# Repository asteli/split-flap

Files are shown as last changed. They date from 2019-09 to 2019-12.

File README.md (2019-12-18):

# split-flap
A mechanical split-flap display in the style of the Solari boards, designed to be modular, manufacturable, and low-cost.

Each module consists of a control PCB, a stepper motor (NEMA 17), mounting bracketry, and wheel made from 3D-printed and laser cut parts, holding 60 custom-printed and laser cut character cards.

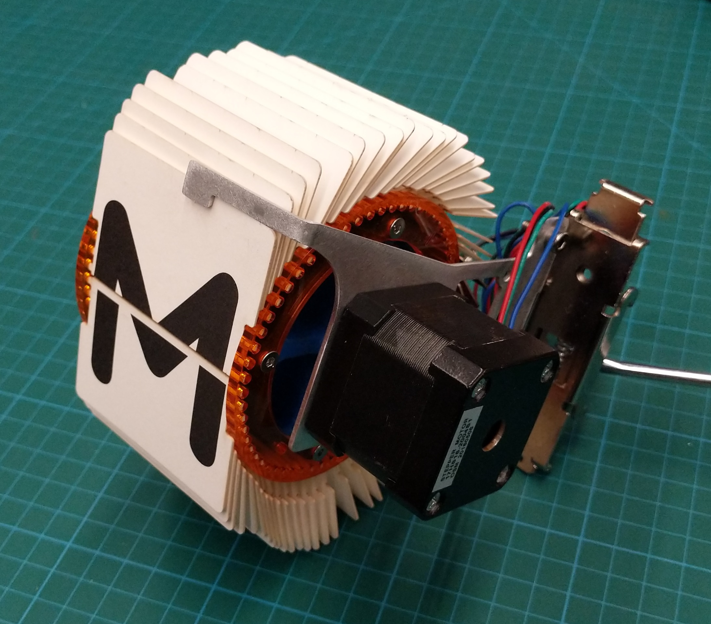
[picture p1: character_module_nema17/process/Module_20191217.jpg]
An assembled module, sans PCB, off of DIN rail.


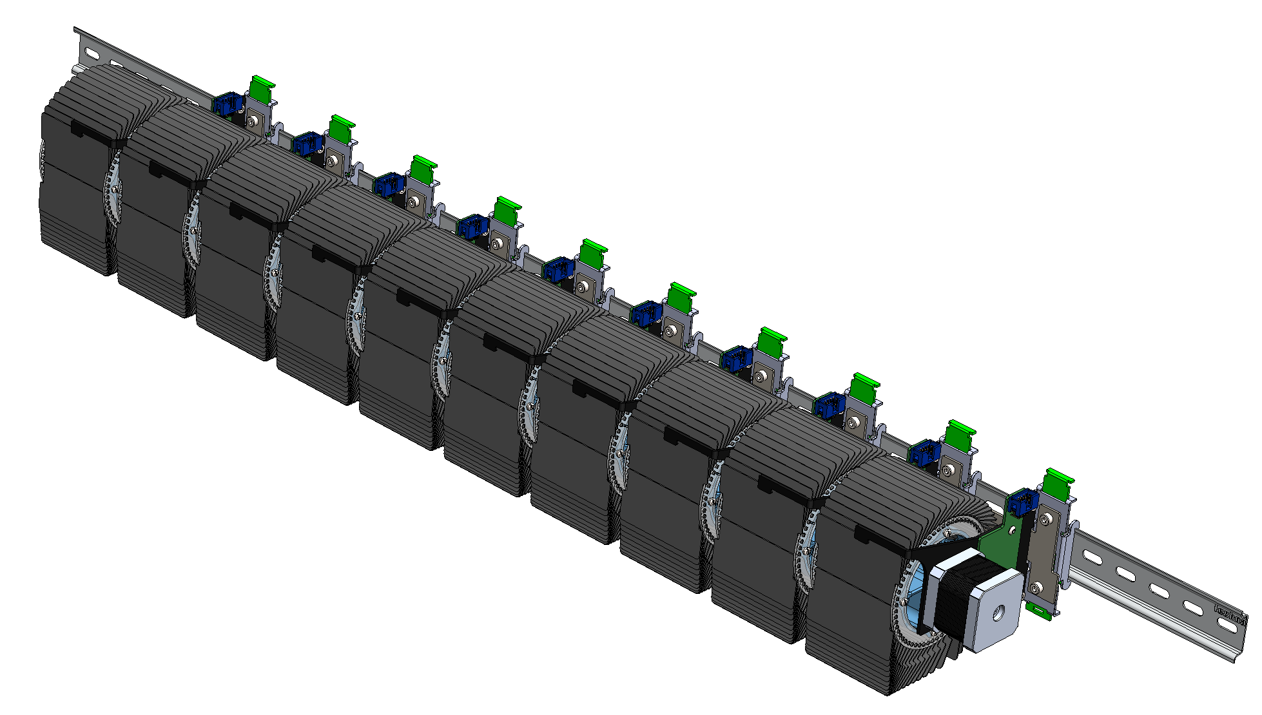
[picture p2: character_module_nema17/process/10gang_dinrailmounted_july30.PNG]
A 10-module wide section of a split-flap display


[Quick video of an early prototype running open-loop](https://youtu.be/AlwcM3Y5v3c) 

The V2 is designed around a NEMA 17 motor, which paradoxically is much cheaper than the NEMA 08. Likely because it enjoys wide use in 3D printers and the like. They cost something like 5-8 USD wholesale. A friend happens to have a few hundred sitting around from an old project, which makes the choice even harder to resist.

The V2 also features a much larger character size (usable character area is roughly 60mm x 60mm -- old flaps were ~35mm wide), and is designed to be DIN rail mountable and powered/controlled via a common rail and bus for simplicity and reliability. The part count has come down significantly -- I've removed the (2) external bearings, as the NEMA 17 motor is large enough that I can trust its bearings to cope with the modest lateral loads involved.

When you are planning on building even 20 of something, every last part counts against you.

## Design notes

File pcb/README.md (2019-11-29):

# PCBA Design Notes:

## Requirements:
	- Small microcontroller (AVR ATMega, STM32F0)
	- Single IDC connector for common bus data and power
		- I2C(sda,scl)[2], V_motor[3], V_logic[2], GND[5]
	- Hall effect sensor for indexing
	- DIP switches to set address
	- Stepper motor driver IC
	- (optional pop) - RST and CALIB switches
	- sundry LEDs
	- PMIC (Vmot -> V_logic (3.3V))
	- PTC or other input protection (we're common bus yo! gotta be careful)
	- ESD and other protection

## Parts Selected:
	MCU 	- ($1.93/1pc) STM32F030C8T6TR 
	DIPSW 	- ($0.98/1pc) 8pos, SMD, TE CONN. 1-1825058-9
	DRIVE 	- ($3.11/1pc) A4988
	PMIC 	- ($0.83/1pc) DC-DC Buck AOZ1282CI (12 -> 3.3V) (investigate cheaper chinese parts at some point)
			- (solution cost $3?)
	HALL 	- ($0.40/1pc) Toshiba TCS40DPR
	LEDs	- ($0.26/1pc) LTST-C190GKT (0603 Green)
			- ($0.26/1pc) LTST-C190KRKT (0603 Red)
	CONN 	- ($1.56/1pc) Molex 0901303112 . 12POS Rectangular header, shrouded+keyed, R/A
				- Alt: 	5-102617-4 TE Connectivity AMPMODU II line, $2.53/1pc
	TACSW 	- ($0.12/1pc) Panasonic EVQ-Q2B03W

	So far we're looking at ~$15 in components? Maybe $5 for the PCB and $5 for assy/board? (Maybe wishful thinking)

## MCU Functionality:
	In no particular order:
		- Listen to I2C, filter incoming messages and display character corresponding to address
		- Calibration functionality - tacsw advances cards until hallsw, zeroes counter, slowly rotates until operator releases button 
		at the index card. index card position stored in NVM.
		- DIPSW translates to address
		- Control registers accessible by I2C in direct-addressed mode. LEDs, calibration, motor settings, character maps
		- Standby current control (or shut off driver IC entirely if that works mechanically and doesn't cause glitching to adjacent 
		characters)
			- This can be accomplished using a couple I/O and voltage divider ladder to get the voltages we want. Will have to tune the resistor values but easy to use 1 I/O to set RUN vs STDBY current.

## MCU I/O Pin Counts:
	- [2] I2C
	- [8] DIP switch configuration
	- [8] A4988 Motor controller (nSleep, step, ms1:3, dir, nEnable, nReset)
	- [2] A4988 V_ref control
	- [2] LEDs
	- [1] User switch
	- [1] Hall sensor

	Looks like ~24 I/O min? Cheapest that'll fit? STM32F030K6T6, with 26 I/O. ($1.62/1pc, CT)

	Next up in the price lineup is STM32F030C8T6TR, with 39 I/O, at a whopping $1.93/1pc, cut tape.

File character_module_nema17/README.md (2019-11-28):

## TODO:
- Build new character flap vector files. Old flap vectors split each character between the front and back of the print, causing character-half registration issues.
- Spec and design module control PCBA
- Print and laser cut new flaps
- Waterjet and bend prototype bracket, validate bracket design

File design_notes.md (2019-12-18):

# SplitFlapClock Design Notes

## December 17, 2019
Waterjet and bent the bracket. Used 0.0615 aluminum, only because that's what was in the scrap bin that was large enough. It's a bit flimsy like that, should use 0.080 at least. Fitment is OK, the arm on top actually seems to have the side-effect of ratcheting the hub, as the flaps sort of deform into a V shape, catching and preventing the hub from rotating backwards. I might keep that.

Torque on the motor seems pretty reasonable, although I could probably move the retention arm out another millimeter and reduce the torque/power requirement/wear on cards (probably).

## December 1, 2019
The KiCad libs available are pretty nice. Haven't had to make any schematic symbols myself yet. Digikey has nice libs available, and the KiCad official lib seems pretty expansive as well. Good job everyone!

## November 29, 2019
Toying with the idea of using the STM32F0 itself to create the stepper waveforms. Sounds trivial but I would need a way to sense phase current. That would potentially reduce the unit cost by $2? The FETs could be quite small at these powers. The issue then is that I would be committing to engineering a motor controller, which... well, maybe let's leave that for the cost optimized version of this module. I do like the idea though.

DIP SW: use int PU res, allow DIP to short to GND. 

## November 28, 2019
Status update:
	- Staying with NEMA 17.
	- Staying with a PCB per module
	- I'm going to use DIP switches to set addresses, because my previous scheme seems like a pain in the ass and the ease of confiuration with DIP switches is worth the extra cents. 

I'm starting the PCB design. Looks fairly simple. Going to be all DIGIKEY parts for this first build, I can try to go and cost optimize (chinese domestic components and assy) later. I wonder if I can find a vendor for the steel plates.

Spec'ing PCB parts is coming along. I'm going to try to get a really solid architecture together before actually building things.

So much of the time I see hardware/firmware/mechanicals being developed independently of each other, but here I have the option of thinking through the entire design, tip to tail, which is nice.

## September 16 2019

CAD for the newest version is mostly done. Have the mounting plate mostly designed up but I am going to simplify the geometry a bit to make it slightly easier to manufacture.

I am also looking at evaluating the 28byj-48 geared stepper motor in conjunction with a uln2003, apparently a popular configuration for small and low power actuation. 
	This motor appears to be quite small and have limited torque. Its max speed is something like 15RPM (0.25 Hz) which is more than fast enough for a split flap display. 

VW has loads of stepper motors he doesn't need. They are not D-flatted, which doesn't mean much in my application. I need to figure out how to size the bore of my hub to be a press fit that doesn't take massive amounts of force to attach/detach. Going slightly loose is an option as I can always use an adhesive (RTV? CA glue?) to retain it if the slip fit is a bit oversize.

## July 30 2019

Looking at using i2c for communications. Assuming 0.5A for 1 module, 7A continuous max amperage for 22AWG, that gives us 14 modules per power conductor pair. So doubling up (2x 24V, 2x PGND) gives us a decent amount of headroom. I want to use IDC connectors, just because fabricating the cable will be as simple as punching down a bunch of connectors on a shared ribbon, and it minimizes passthrough/daisy-chain failure modes. I was looking at a serial retransmit scheme like WS2812s or APA102s but I think this will be more reliable.

Question is how to assign i2c addresses to submissive devices. Scheme is as follows:

There _is_ a daisy chained "strobe" signal -- wait that doesn't work because we're using common bus IDC and ugh

OK how about maybe using prop delay? Naw sounds flakey.

Could do the classic i2c dip-switch or solder-blob jumper thing. Could do 6 bits, 64 permutations... should be good enough for anyone, right?

Tac switch on each device that when pushed, queries the bus for taken addresses, then assigns itself to the first open slot. Then saves its address to eeprom. Need an address reset mechanism, maybe by resetting uC with the "address set" switch depressed.

Then when the primary controller powers up, it scans the bus for available secondaries and assumes that they're physically in order from left to right.

Doing i2c means that a raspi or something can be in charge of setting all the things, which means application code can be in python or something. Plug a LORAN modem into the UART and bam, long distance wireless.

Only needs to be set up once. We can also have modules ident using their built in single-character displays.

Issue in the model: my SOT23 hall-effect sensor sits about 5mm away from the outer surface of the flap disk. I would much rather it be something like 2mm. I guess I could just use a longer magnet... was spec'ing a 1/16" (Thick) x 1/8" (Diam) magnet before, could use a 1/8"x1/8" and that closes the gap by 0.3175/2 = 1.56 ish mm. goes down to 3.5mm. more reasonable. I think I can live with that. OK crisis averted. I am slightly worried about magnetizing my screws, in which case the hall effect sensor could pick up the screws as well as the magnet. Maybe use SS screws there. Or don't magnetize them I guess.

Going to design a plate that links up with the DIN clip. It will set spacing and add a little bit of torsional stability to the assembled modules.

## July 29
I think I want to build the character displays in 4 or 5-gang modules. 20-gang is going to be super huge. 4-gang seems like a fun clock sized size. 5 would also work.
This would also be a good size for having one PCB control a number of them and not have insane looking harnesses running around. 

Local VMOT24 -> 5/3.3V for logic.

Connectivity:
UART
Ethernet
Power -- possible to do PoE? What's our PD? It's easy and cheap to do the typical powerpole terminals however.

TODO:
	- Retention tab

	- Model module mounting solution
		- DIN rail brackets?
		- DIN rail
	- Hall effect sensr
		- p/n
		- model
		- location
		- magnet location
	- PCB
		- location
		- functionality
		- connectivity

## June 3:

Other bearings came in. Pressed all the stuff together, forgot to align the flat on the motor shaft, broke the spokes out of the hub. 

That aside, there's still massive eccentricity in my otherwise round parts. I think I probably need to orient them such that they print with the rotational axis nearly straight up, despite the risk involved.

Other issues: Clearance between rotating parts. The further the material gets from the rotation axis or the fixing bearing, the more likely it is to rub. Keep clearances wide open if it doesn't affect functionality. No lost pride in having some air in the design.

The motor is indeed strong enough to rotate the display, but just barely. Eccentricity causes uneven lateral forces on the shaft that result in binding at one part of the rotation. Solution? Reprint hub.

Bearing seat were also rather tight. They did eventually fit but I think I want to add another 50 micron or more to the radius of the large seats. It's easy to get a bearing not to spin in a seat, lot easier than removing material to get it to press in.

Also, adding deep chamfers (1+ mm ) to the first edge of the bearing seat should help with getting them pressed in perpendicular in the first place. Use a press...

There was minimal issue putting the inserts in. May be a good idea to deepen the bores they go into. Chamfer couldn't hurt.

Oversizing the motor slot by 100um. Can glue it in just as easily. Little CA'll do ya.

Going 100um oversize on the bearing bore (up from 50um oversize). 

Added a little recess for a tiny chunk of retroreflector to sit in.

Todo on the enclosure:
Find a way of affixing the leaf that doesn't look like jank
Remove the slot and tab stuff from the front.
Enlarge the hole for the motor connector access.
Get rid of the leaf spring entirely and just use the acrylic to detain the flaps.

Todo on the motor mount:
Bore deeper for the inserts
Chamfer the outside edge at the far end of the motor

Todo on Flaps:
Generate Template for cutting

Mid July:
Ditched the old design. The motor was a bit small for what it was doing, and worse, NEMA 08 motors are expensive. I'm moving to a NEMA 17 motor, which can be had for $5 a piece perhaps (and VW has a lot, 400 something of these motors just sitting around).

Redesigned, removing the near and far end bearings -- the bearings in the motor itself are now big enough to handle the radial loads. This brings down part count significantly.
Also I'm going to ditch the per-module enclosure, and modify the design such that the motors nest inside the adjacent hubs. Per-module structure goes from:

Acrylic enclosure
Motor mount block
Motor mount bearing
Motor NEMA 08
Hub
Hub disks
Flaps
Far end bearing
Far end bearing block

To:
Sheet metal bracket
Motor NEMA 17
Hub
Hub disks
Flaps

Also I'm downsizing the flaps disks from 1/8" acrylic down to 1/16" because it's cheaper and the loads involved are very small. This will allow me to squeeze PHSCHS or SHCS screws in to fasten the disks, meaning that I don't have to counter sink those self-tapping M2.5 clearance holes.

## May 29

Loaded the models into preform. I tweaked the printed parts to use brass M3 threaded inserts instead of screwing directly into the plastic. Had to increase the size of a couple parts in order to make that work.

I'm going to screw directly to the hub to attach the acrlic flap retainer disks.

Laying out the components in Preform, I'm making sure to orient the parts to keep most if not all of the support structure touchpoints out of the bearing areas so that we don't get interference when I try to press the bearings in.

## May28

Added the encoder. Shortened the flaps just slightly, looks like it can't jam now. Not sure about what material to use for the flaps still. Acrylic likely too brittle. Thinking delrin or PET?

Ordered all materials. Came out to $200. Haven't worked out the spring thing bit yet. Considering harvesting the steel clip off of a pen to make the first article.

## May 27 2019

Aspect ratio of the flaps is interesting. Making them long makes the space needed to do the angle reversal after the card is displayed bigger, and thus drives part of package size.

I'm noticing that certain design choices are ... convergent. Like having the tabs on the sides of the flaps, or having a certain aspect ratio in order to get the packaging to make sense. (taller flaps mean the whole enclosure has to get taller to give them space at the bottom of the loop)

I'm envisioning an even less expensive design for light duty use that uses DC gearmotors and a grey code optical encoder printed on the side of the hub. uC on the back has just one FET to turn the motor on, and reflectivity pickups. If sensors don't see the right code for the commanded character, spin the motor.

The bearings are massive overkill as well. For a clock sort of function a set of low friction plastic or brass bushings would work great. Very little load. I'm going to use ball bearings because they're what I know. Also they look pretty slick.

I'm not quite sure yet how I want to do the control. One way would be to have a separate controller on each module and daisy chain them a la serially addressable LED chains. You'd need a host somewhere that could spit UART at the modules. Do we want checksums here? Is that overkill? There are super low-tech ways to go about the control. If one was willing to index using an encoder of some kind, it's certainly possible to use basic logic gates and a DC gearmotor to servo to a position encoded as binary or BCD over 6 logic bits. Very 80s. Maybe next rev.

I'm going to need to cut the lower lip of the front opening on the enclosure down low enough that the flaps can't jam up against it. sort of a liability as it stands now, the rotor could push the flaps down into it and sieze the mechanism. Maybe shorten the flaps ... again ... if the enclosure cut looks untenable.

I just realized I can install the encoder or reflectometer or whatever -- the positioning thingy into the far side bearing block. Got loads of space there and I can make a cut in the side of the casing just like for the motor wires. Don't think there's enough space to put an actual full encoder on there right now, although I could distribute the sensors throughout the disk around the bearing. But that's an unwieldy solution, to say the least.

Rotate the bearing block holes 180 and put two screw holes in the block to attach a PCB, add corresponding void in the LH enclosure plate, run wires to the PCB out back. Echo Zulu. Reflecto-dot can go on the hub itself, or optionally the disk. Each one could probably benefit from calibration at time of programming.

### Questions:

The stepper motor I'll probably be using is a NEMA 8 (0.8" square section), with a 1.8 degree full step size. That doesn't really line up nicely with the 6 degree increments between symbol changes. I can use microstepping to even out the rotation. I might have to leave the motors on all the time to keep the rotor at an unnatural resting spot between steps. Also possible that backlash in the mechanism will absorb the last fraction of a rotation after the stepper is powered off. If it ends up being an issue I may have to bite the proverbial bullet and go up in motor size up to a NEMA11 to get a stepper with an 0.9 degree step size. While not exactly a clean divisor, that gives me nearly 7 steps per symbol change. It would also make the entire mechanism a lot bigger. Boo.

How to size tab-and-slot construction for the acrylic enclosure? Can I use nominal dimensions and hope that the laser cutter's kerf takes care of the clearance for me?

What about sizing bores for bearings? I don't know how far off-nominal the housings are going to be. Does it make sense to oversize the bores so that there's maybe a bit of slop, then to fill it in with adhesive? Or to leave it nominal dimension and try and press-fit them? Will that crack the printed plastic parts?

How much bending compliance can I expect from the flaps? Is the retention mechanism that we're using to do the "detent" more reliant on the flap bending or the retention tab bending? Can I use the enclosure itself to do the flap detention?

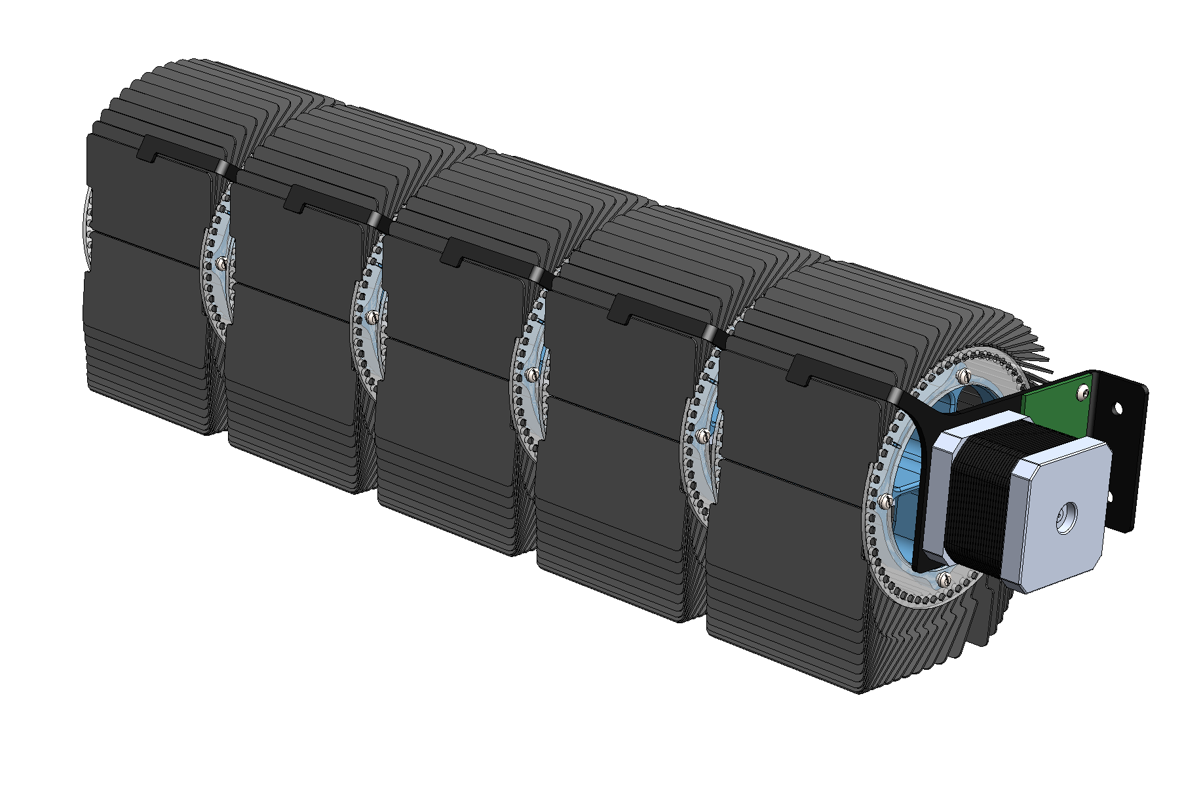
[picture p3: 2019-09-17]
character_module_nema17/process/5gang_motorside_20190729.PNG

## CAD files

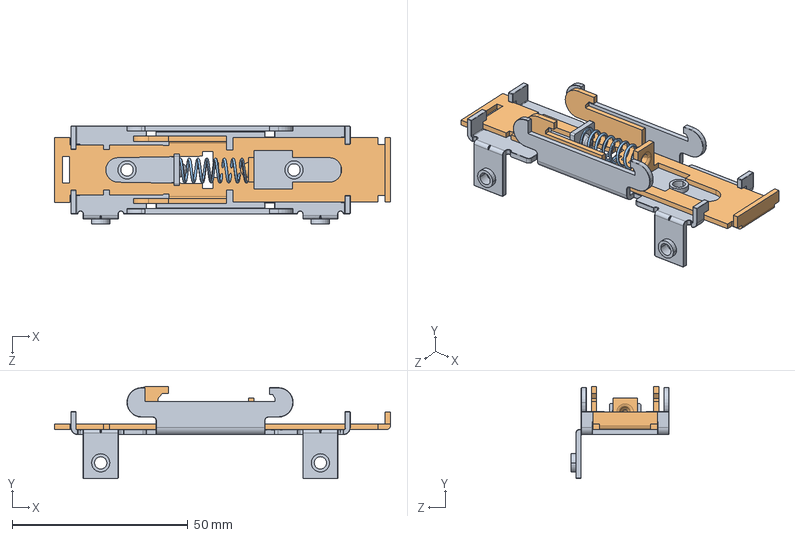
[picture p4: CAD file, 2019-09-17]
character_module_nema17/DINM30/Clip, DIN, Winford DINM30.SLDASM
95.6 x 26.3 x 27.9 mm
DINM30-Clip.step
DINM30-Shell.step
DINM30-Spring.step

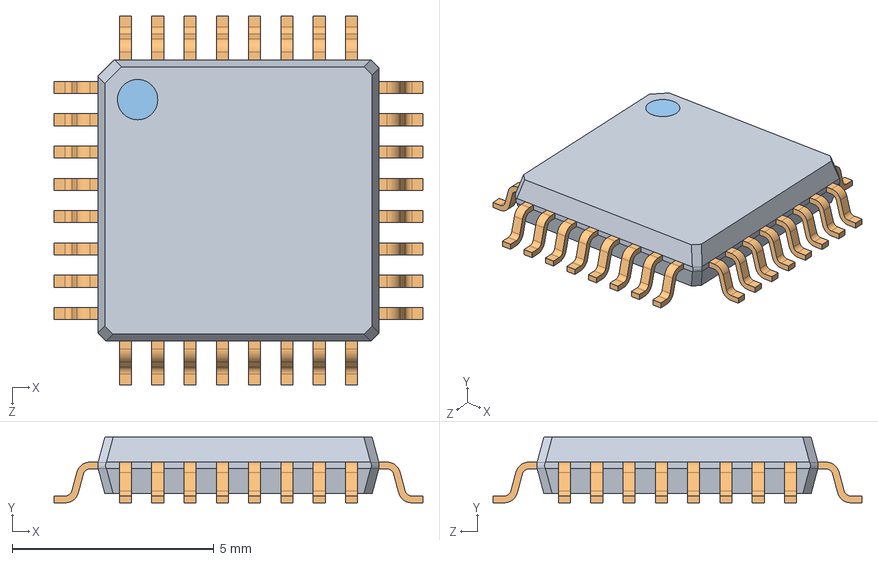
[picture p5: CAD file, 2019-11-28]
character_module_nema17/Electrical Components/LQFP32/User Library-LQFP32-2.sldasm
9.14 x 1.63 x 9.14 mm
User Library-LQFP32-2_case
User Library-LQFP32-2_pin x 32
User Library-LQFP32-2_circle

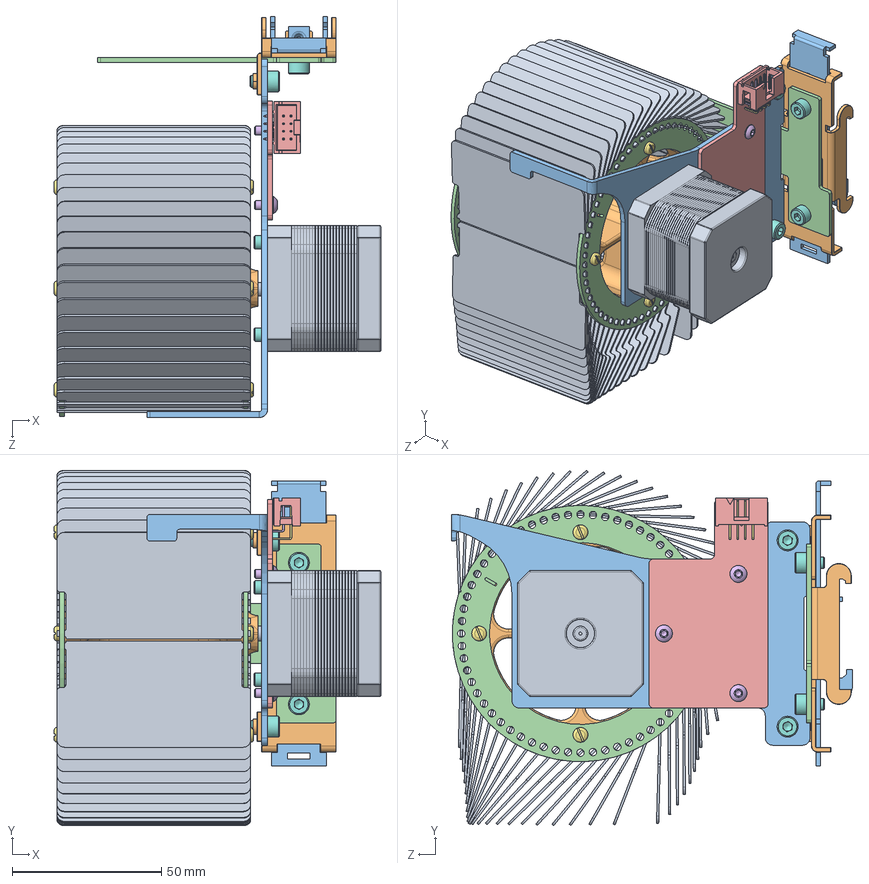
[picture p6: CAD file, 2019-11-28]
character_module_nema17/Subassembly, Character Module.SLDASM
109.7 x 119.3 x 134.6 mm
Motor, Stepper, Nema 17
Hub, Flap Carrier
Bracket, Motor Mount
Disk, Flap Retainer x 2
PCB, Local Driver Board, Outline
socket button head cap screw_am x 3
pan head tapping screw_am x 8
socket head cap screw_am x 8
Split Flap x 60
DINM30-Clip.step
DINM30-Shell.step
DINM30-Spring.step
71965_Y08.stp
71953_X03.stp x 4
71953_X04.stp x 4
User Library-LQFP32-2_case
User Library-LQFP32-2_pin x 32
User Library-LQFP32-2_circle
SOT-23
Plate, Module Spacer

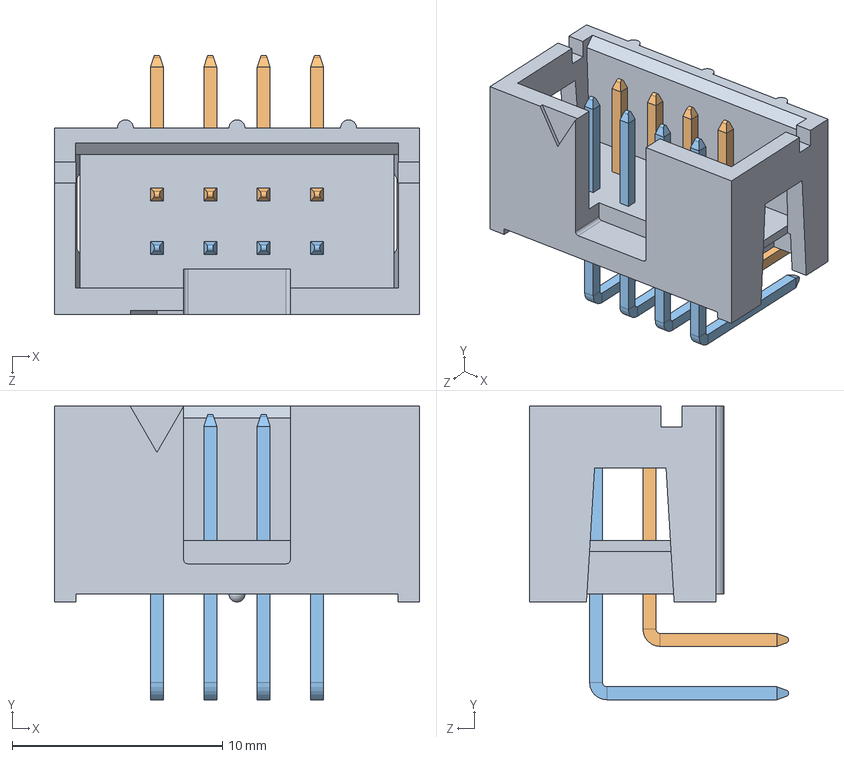
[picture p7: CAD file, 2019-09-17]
character_module_nema17/Connector/Connector, Header IDC, 8 Position, Right Angle, Shrouded, 75867_y32_asm.SLDASM
17.4 x 14.0 x 12.3 mm
71965_Y08.stp
71953_X03.stp x 4
71953_X04.stp x 4

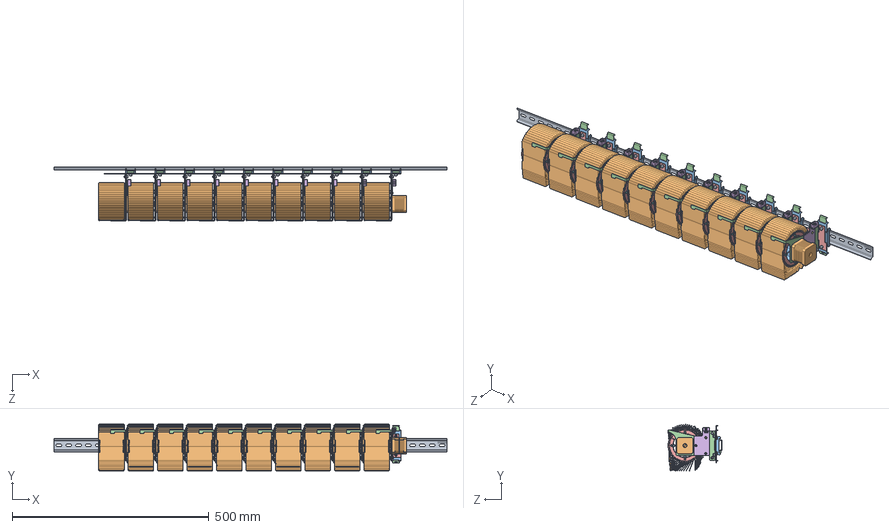
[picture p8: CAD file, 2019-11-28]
character_module_nema17/Assembly, Character Display.SLDASM
1000.0 x 119.3 x 137.7 mm
DIN Rail, 1m, TECHNA_TTEC CA701
Motor, Stepper, Nema 17 x 10
Hub, Flap Carrier x 10
Bracket, Motor Mount x 10
Disk, Flap Retainer x 20
PCB, Local Driver Board, Outline x 10
socket button head cap screw_am x 30
pan head tapping screw_am x 80
socket head cap screw_am x 80
Split Flap x 600
DINM30-Clip.step x 10
DINM30-Shell.step x 10
DINM30-Spring.step x 10
71965_Y08.stp x 10
71953_X03.stp x 40
71953_X04.stp x 40
User Library-LQFP32-2_case x 10
User Library-LQFP32-2_pin x 320
User Library-LQFP32-2_circle x 10
SOT-23 x 10
Plate, Module Spacer x 10

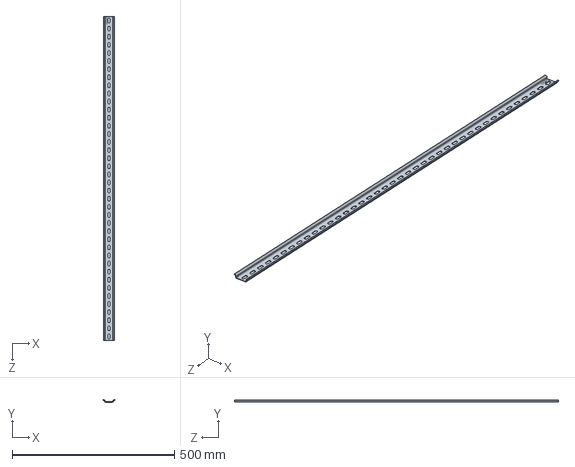
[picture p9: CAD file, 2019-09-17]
character_module_nema17/DIN Rail/DIN Rail, 1m, TECHNA_TTEC CA701.SLDPRT
35.0 x 7.50 x 1000.0 mm

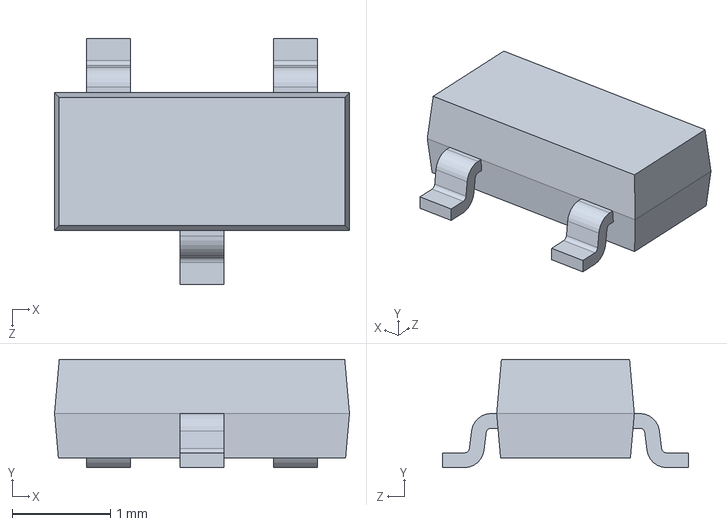
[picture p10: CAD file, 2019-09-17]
character_module_nema17/Electrical Components/SOT23/SOT-23.SLDPRT
3.00 x 1.10 x 2.50 mm

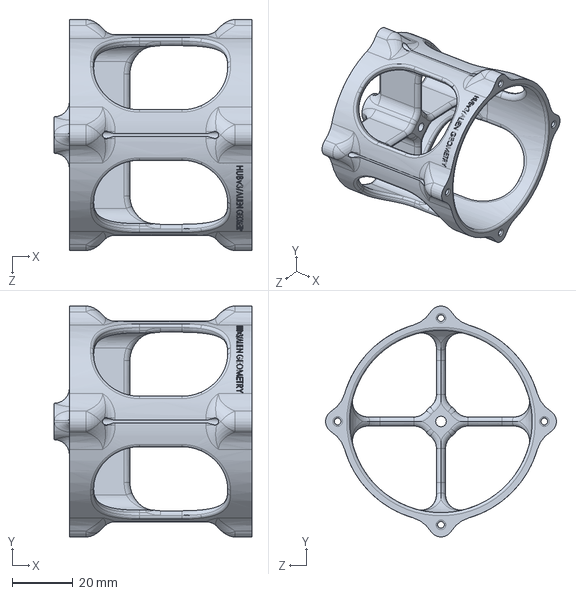
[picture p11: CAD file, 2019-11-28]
character_module_nema17/Hub, Flap Carrier.SLDPRT
65.0 x 76.0 x 76.0 mm

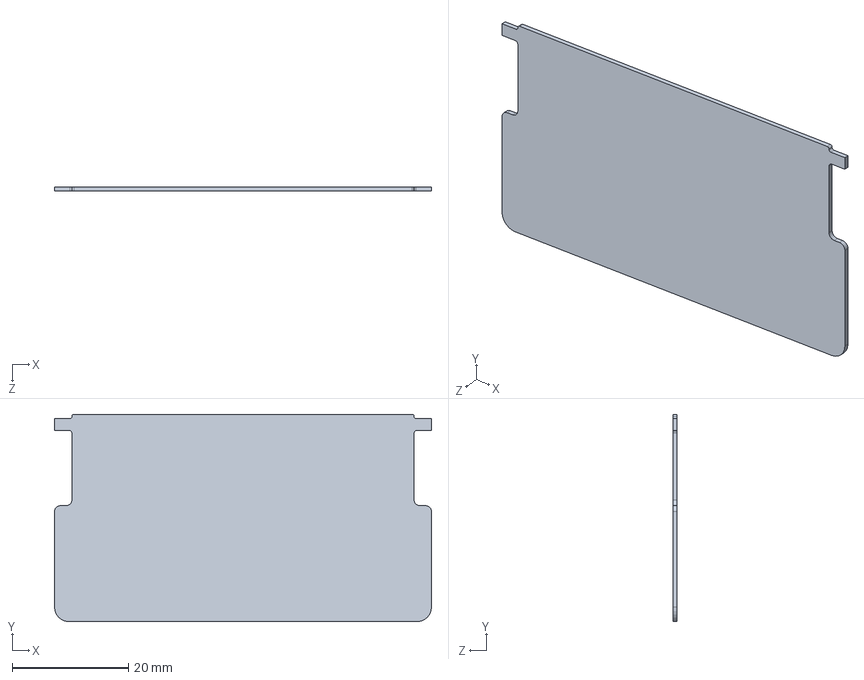
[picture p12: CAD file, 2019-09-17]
character_module_nema17/Split Flap.SLDPRT
65.0 x 35.8 x 0.762 mm

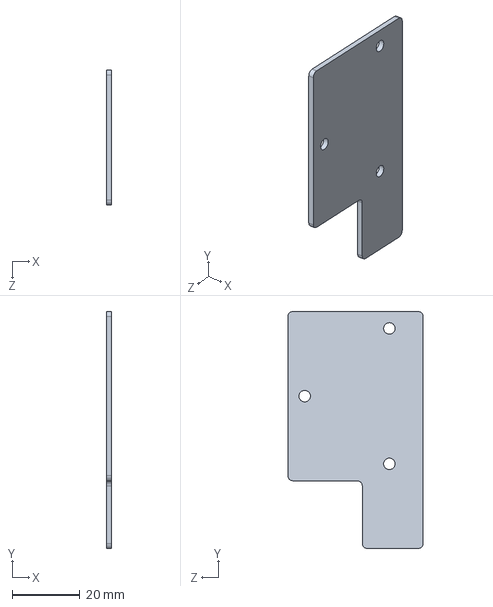
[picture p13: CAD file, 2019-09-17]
character_module_nema17/PCB, Local Driver Board, Outline.SLDPRT
1.60 x 70.0 x 40.0 mm

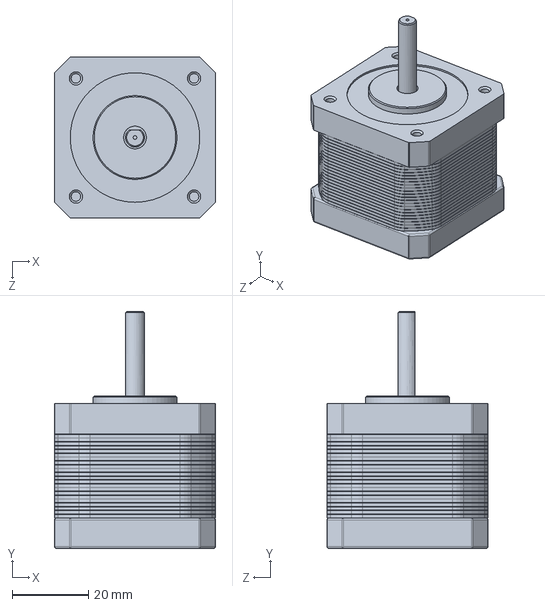
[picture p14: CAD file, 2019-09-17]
character_module_nema17/Motor, Stepper, Nema 17.SLDPRT
42.3 x 62.2 x 42.3 mm

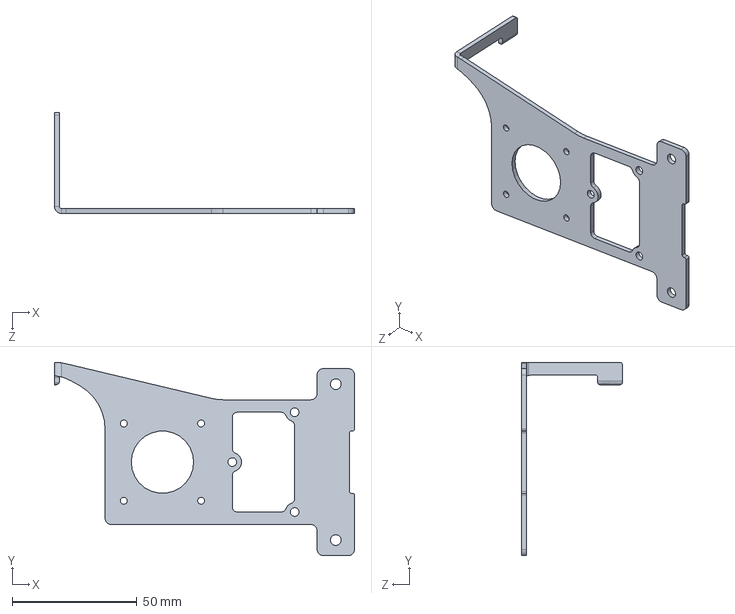
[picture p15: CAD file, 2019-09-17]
character_module_nema17/Bracket, Motor Mount.SLDPRT
120.3 x 77.5 x 40.5 mm

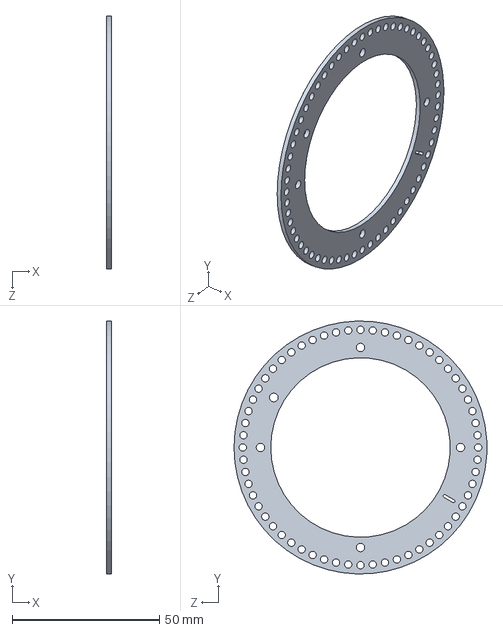
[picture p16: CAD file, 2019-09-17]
character_module_nema17/Disk, Flap Retainer.SLDPRT
1.59 x 86.0 x 86.0 mm

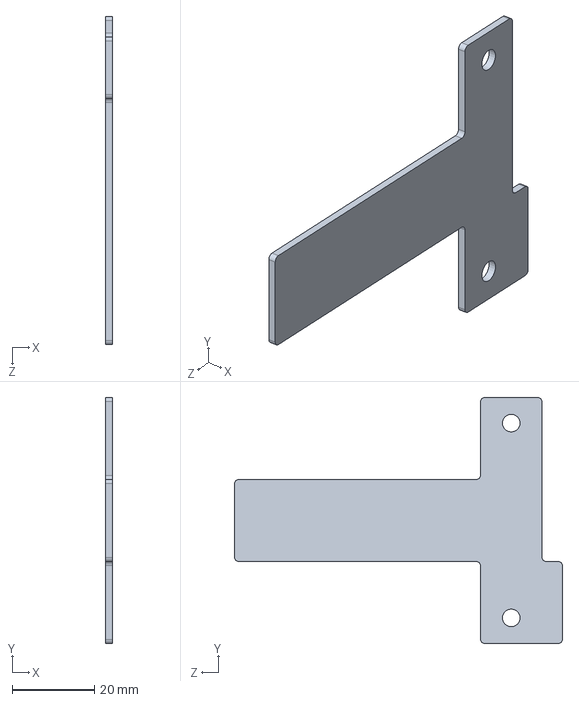
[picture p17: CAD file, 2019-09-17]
character_module_nema17/Plate, Module Spacer.SLDPRT
1.59 x 60.0 x 80.0 mm

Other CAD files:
character_module_nema17/Electrical Components/LQFP32/User Library-LQFP32-2_pin.sldprt
character_module_nema17/Electrical Components/LQFP32/User Library-LQFP32-2_circle.sldprt
character_module_nema17/Electrical Components/LQFP32/User Library-LQFP32-2_case.sldprt
character_module_nema17/Connector/75867_y32_asm.stp

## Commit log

2019-09-17 Adding the V2 files to repo
    [75867_y32_asm.stp, Assembly, Character Display.SLDASM, Bracket, Motor Mount.SLDPRT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]
2019-11-28 Added PCBA markdown readme. Created top-level todo.
2019-11-28 mod pcba readme.
    [Assembly, Character Display.SLDASM, Hub, Flap Carrier.SLDPRT, Subassembly, Character Module.SLDASM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]
2019-11-29 updated pcba README.md
2019-11-29 added kicad PCB files
    [sfd_module_ctrl.kicad_pcb, sfd_module_ctrl.sch]
2019-12-01 schematic progress, added stm32cubeMX generated chip config
    [sfd_module_ctrl.sch]
2019-12-18 Added in-process photo, updated design_notes.md
    [sfd_module_ctrl.sch]
